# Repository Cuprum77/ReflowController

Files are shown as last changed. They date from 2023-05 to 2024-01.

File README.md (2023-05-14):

# Reflow Controller

This is my own take at building my own reflow oven. This repo will contain all the documentation, code and hardware design files.

## Oven

As there are no easily available small oven here in Norway for a reasonable price, I settled on the [Point PMO16BL](https://www.power.no/kjoekkenmaskiner/kjoekkenapparater/miniovn-og-frittstaaende-platetopp/point-pmo16bl-miniovn/p-1136808/) from Power, a Norwegian electronics store. It's a 16L oven with a max temperature of 230°C. However I do believe we can get it to go higher than that.

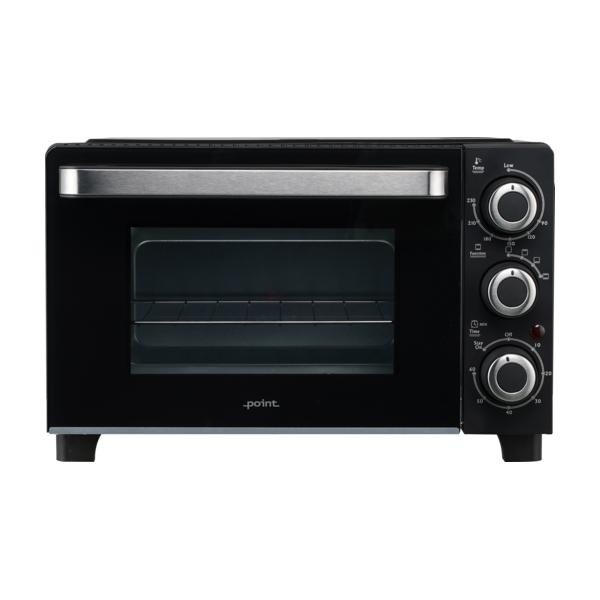
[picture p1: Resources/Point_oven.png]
Oven


Through coupons and discounts I managed to get one brand new from a store for as little as 291 NOK, which as of now (2023-05-14) is about 20.54 USD.

## Controller

The controller itself is designed to be as simple as possible and have to navigate around the still ongoing chip shortage. It features an RP2040 microcontroller, a 1.28" circular LCD display, a button, and the option for a rotary encoder as well as up to 3 thermocouple inputs and 3 relays for controlling the oven.

However, it is not capable of receiving the thermocouples straight in, even though it would have been more practical. This is due to the chips chosen were not available on their own, but only as a breakout board. So to save time and effort, I decided against simply moving the chips over to a main board, and instead just use the breakout boards as is. An advantage of this approach, is the potential for a solderless experience if more thermocouples are needed in the future.

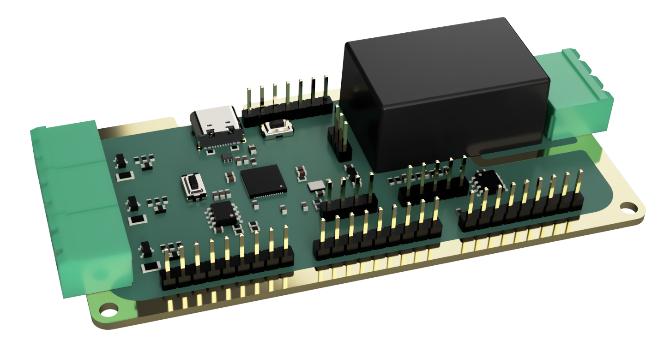
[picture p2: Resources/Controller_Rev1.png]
Controller


The controller will also feature an onboard EEPROM for storing the heat profiles and settings as well as a USB-C connector for programming. The board can be powered directly from mains through a large plug in connector.

## Software

## License
This project is licensed under the CERN Open Hardware Licence v2 - Strong Reciprocity (CERN-OHL-S-2.0). See [LICENSE](./LICENSE) for more information.

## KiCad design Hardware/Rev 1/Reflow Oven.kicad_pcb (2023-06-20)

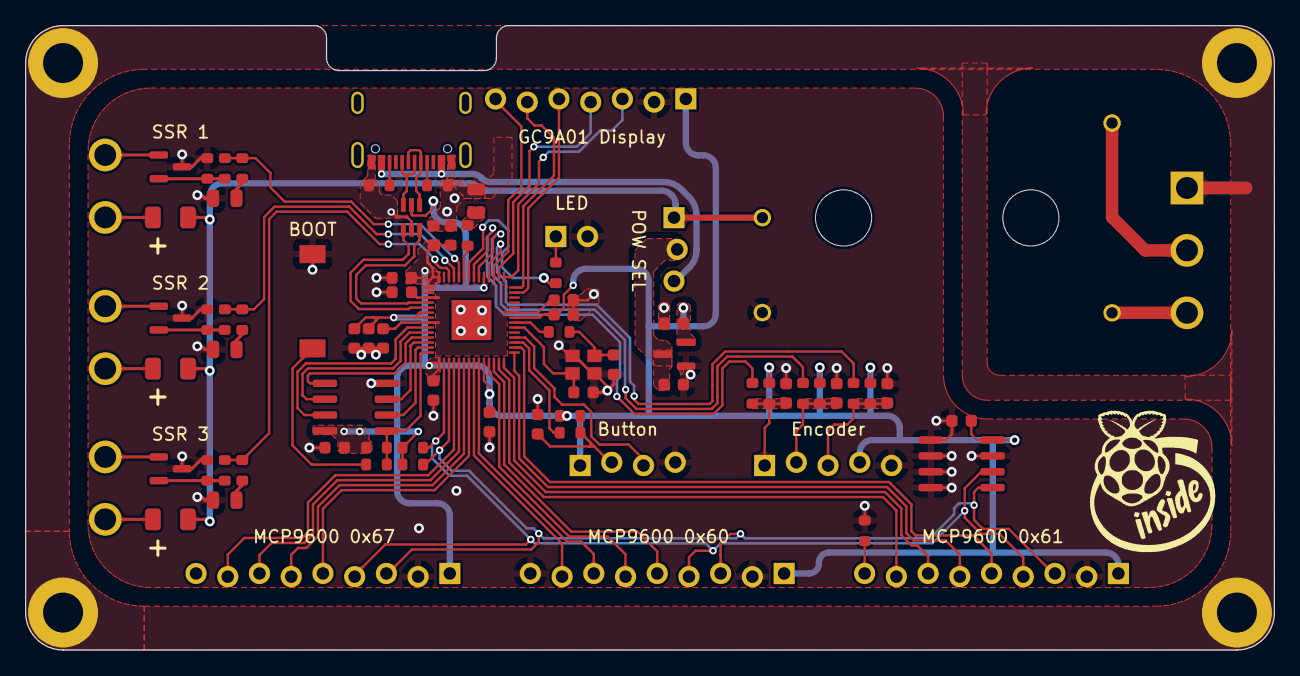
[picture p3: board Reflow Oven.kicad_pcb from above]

Board: 2 copper layers, 100.0 x 50.0 mm, 83 parts (0 on the bottom side), 73 nets.

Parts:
C1, C2, C3, C4: 10n; C_0603_1608Metric
C5, C8, C10, C11, C12, C13, C14, C16, C17, C18, C20: 100n; C_0603_1608Metric
C6, C7: 8p; C_0603_1608Metric
C9, C19: 1u; C_0603_1608Metric
C15: 10u; C_0603_1608Metric
C21: 2u2; C_0603_1608Metric
D1, D2, D3, D4: Red; D_0805_2012Metric
F1, F2, F3: Fuse; Fuse_1206_3216Metric
H1, H2, H3, H4: M3; MountingHole_3.2mm_M3_DIN965_Pad
IC1: MCP1792T; SOT-23
J1: SW; PinHeader_1x04_P2.54mm_Vertical
J2: ENC; PinHeader_1x05_P2.54mm_Vertical
J3, J4, J5: Adafruit 4101; PinHeader_1x09_P2.54mm_Vertical
J6: GC9A01 1.28" TFT; PinHeader_1x07_P2.54mm_Vertical
J7: 2350513-3
J8, J9, J10: 2350513-2
J11: USB4110-GF-A_REVB; USB_C_Receptacle_GCT_USB4105-xx-A_16P_TopMnt_Horizontal
J12: POW_SEL; PinHeader_1x03_P2.54mm_Vertical
J13: Conn_01x02; PinHeader_1x02_P2.54mm_Vertical
P1: IRM015
Q1, Q2, Q3: IRLML2060; SOT-23
R1, R23, R24: 2k2; R_0603_1608Metric
R2, R3, R4, R5, R6, R7, R8, R9, R14, R17, R20: 10k; R_0603_1608Metric
R10, R11: 5k1; R_0603_1608Metric
R12, R15, R18, R26, R27: 270; R_0603_1608Metric
R13, R16, R19: 100; R_0603_1608Metric
R21, R22: DNF; R_0603_1608Metric
R25: 1k; R_0603_1608Metric
SW1: DNF; PTS636 SM25J SMTR LFS
U1: USBUF02W6; SOT65P210X110-6N
U2: W25Q16JV; SOIC-8_3.9x4.9mm_P1.27mm
U3: FT24C04A; SOIC-8_3.9x4.9mm_P1.27mm
U4: RP2040; QFN-56-1EP_7x7mm_P0.4mm_EP3.2x3.2mm
Y1: 12MHz; Crystal_SMD_2520-4Pin_2.5x2.0mm

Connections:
+1V1: C5.1, C8.1, C9.1, U4.23 (DVDD), U4.45 (VREG_VOUT), U4.50 (DVDD)
+3V3: C10.1, C11.1, C12.1, C13.1, C14.1, C16.1, C17.1, C18.1, C19.1, C20.1, C21.1, IC1.2, J1.1, J2.4, J3.1, J4.1, J5.1, J6.1, R2.1, R3.1, R5.1, R8.1, R22.2, R23.1, R24.1, U1.5 (3V3), U2.8 (VCC), U3.8 (VCC), U4.1 (IOVDD), U4.10 (IOVDD), U4.22 (IOVDD), U4.33 (IOVDD), U4.42 (IOVDD), U4.43 (ADC_AVDD), U4.44 (VREG_IN), U4.48 (USB_VDD), U4.49 (IOVDD)
+5V: F1.1, F2.1, F3.1, J12.1, P1.1 (V+)
/ALARM1A: J3.5, U4.7 (GPIO5)
/ALARM1B: J4.5, U4.16 (GPIO13)
/ALARM1C: J5.5, U4.12 (GPIO9)
/ALARM2A: J3.6, U4.6 (GPIO4)
/ALARM2B: J4.6, U4.15 (GPIO12)
/ALARM2C: J5.6, U4.11 (GPIO8)
/ALARM3A: J3.7, U4.5 (GPIO3)
/ALARM3B: J4.7, U4.14 (GPIO11)
/ALARM3C: J5.7, U4.9 (GPIO7)
/ALARM4A: J3.8, U4.4 (GPIO2)
/ALARM4B: J4.8, U4.13 (GPIO10)
/ALARM4C: J5.8, U4.8 (GPIO6)
/Button Filter/SW_OUT: R9.1, U4.17 (GPIO14)
/ENC_A: C1.1, J2.1, R2.2, R4.2
/ENC_B: C2.1, J2.2, R3.2, R6.2
/ENC_Filter/ENC_A_OUT: R4.1, U4.35 (GPIO23)
/ENC_Filter/ENC_B_OUT: R6.1, U4.34 (GPIO22)
/ENC_Filter/ENC_SW_OUT: R7.1, U4.32 (GPIO21)
/ENC_SW: C3.1, J2.3, R5.2, R7.2
/LCD_CS: J6.6, U4.28 (GPIO17)
/LCD_D/C: J6.5, U4.27 (GPIO16)
/LCD_MOSI: J6.4, U4.30 (GPIO19)
/LCD_RST: J6.7, U4.31 (GPIO20)
/LCD_SCK: J6.3, U4.29 (GPIO18)
/Live: J7.2, P1.4 (L)
/MOSFET_1: R12.1, R13.1, U4.40 (GPIO28_ADC2)
/MOSFET_2: R15.1, R16.1, U4.38 (GPIO26_ADC0)
/MOSFET_3: R18.1, R19.1, U4.39 (GPIO27_ADC1)
/MOSFETs/SSR_1: J8.2, Q1.1 (D)
/MOSFETs/SSR_1_COM: F1.2, J8.1
/MOSFETs/SSR_2: J9.2, Q2.1 (D)
/MOSFETs/SSR_2_COM: F2.2, J9.1
/MOSFETs/SSR_3: J10.2, Q3.1 (D)
/MOSFETs/SSR_3_COM: F3.2, J10.1
/Microcontroller Alarm/LED_ACTIVE: R26.2, U4.37 (GPIO25)
/Microcontroller Alarm/LED_FRONT: R27.2, U4.36 (GPIO24)
/Microcontroller Alarm/QSPI_SCLK: U2.6 (CLK), U4.52 (QSPI_SCLK)
/Microcontroller Alarm/QSPI_SD0: U2.5 (DI(IO0)), U4.53 (QSPI_SD0)
/Microcontroller Alarm/QSPI_SD1: U2.2 (DO(IO1)), U4.55 (QSPI_SD1)
/Microcontroller Alarm/QSPI_SD2: U2.3 (IO2), U4.54 (QSPI_SD2)
/Microcontroller Alarm/QSPI_SD3: U2.7 (IO3), U4.51 (QSPI_SD3)
/Microcontroller Alarm/QSPI_SS: R21.2, R22.1, U2.1 (~CS), U4.56 (QSPI_SS)
/Microcontroller Alarm/SW_LED: J1.3, U4.18 (GPIO15)
/Microcontroller Alarm/USB_D+: U1.1 (D+), U4.47 (USB_DP)
/Microcontroller Alarm/USB_D-: U1.3 (D-), U4.46 (USB_DM)
/Microcontroller Alarm/XIN: C6.2, U4.20 (XIN), Y1.1
/Microcontroller Alarm/XOUT: R25.1, U4.21 (XOUT)
/Neutral: J7.3, P1.3 (N)
/SCL: J3.3, J4.3, J5.3, R24.2, U3.5 (SDA), U4.3 (GPIO1)
/SDA: J3.4, J4.4, J5.4, R23.2, U3.6 (SCL), U4.2 (GPIO0)
/SW: C4.1, J1.2, R8.2, R9.2
/USB/USB_PRE_D+: J11.A6 (D+), J11.B6 (D+), U1.6 (D+)
/USB/USB_PRE_D-: J11.A7 (D-), J11.B7 (D-), U1.4 (D-)
Earth: H1.1, H2.1, H3.1, H4.1, J7.1
GND: C1.2, C2.2, C3.2, C4.2, C5.2, C6.1, C7.1, C8.2, C9.2, C10.2, C11.2, C12.2, C13.2, C14.2, C15.2, C16.2, C17.2, C18.2, C19.2, C20.2, C21.2, D1.1 (K), D2.1 (K), D3.1 (K), D4.1 (K), IC1.1, J1.4, J2.5, J3.2, J4.2, J5.2, J5.9, J6.2, J11.A1/B12 (GND), J11.B1/A12 (GND), J13.2, P1.2 (V-), Q1.3 (S), Q2.3 (S), Q3.3 (S), R1.1, R10.2, R11.2, R14.2, R17.2, R20.2, SW1.1, U1.2 (Grd), U2.4 (GND), U3.1 (A0), U3.2 (A1), U3.3 (A3), U3.4 (GND), U3.7 (WP), U4.57 (GND), Y1.2, Y1.4
unnamed: C7.2, R25.2, Y1.3
unnamed: D1.2 (A), R12.2
unnamed: D2.2 (A), R15.2
unnamed: D3.2 (A), R18.2
unnamed: D4.2 (A), R26.1
unnamed: J4.9, R1.2
unnamed: J11.A5 (CC1), R10.1
unnamed: J11.B5 (CC2), R11.1
unnamed: C15.1, IC1.3, J12.2
unnamed: J13.1, R27.1
unnamed: Q1.2 (G), R13.2, R14.1
unnamed: Q2.2 (G), R16.2, R17.1
unnamed: Q3.2 (G), R19.2, R20.1
unnamed: R21.1, SW1.2
VBUS: J11.A4/B9 (VBUS), J11.B4/A9 (VBUS), J12.3

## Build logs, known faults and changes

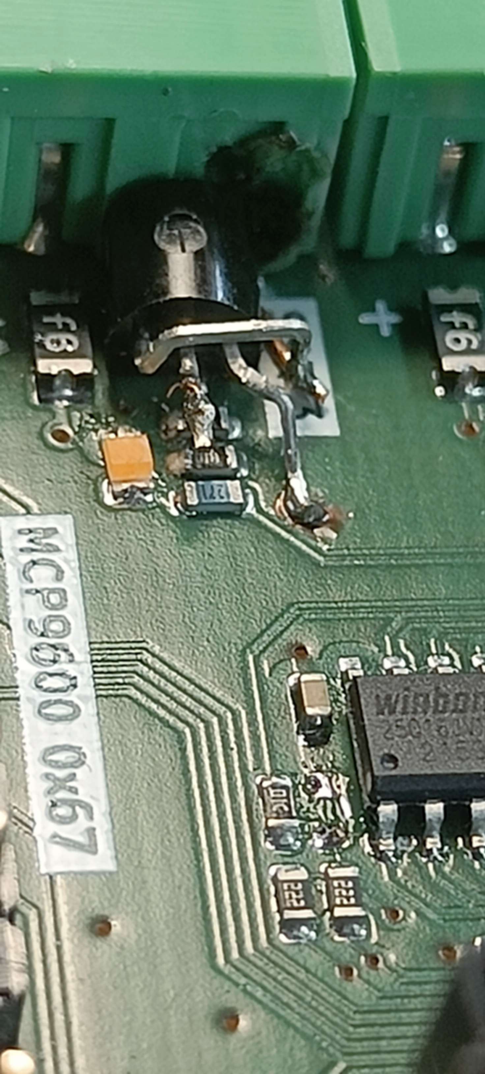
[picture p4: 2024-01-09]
Resources/rev1_fix.jpg

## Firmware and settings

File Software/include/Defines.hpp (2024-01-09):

// This is a header guard. It prevents the file from being included more than once.
#pragma once

/***
 *      ____  _           
 *     |  _ \(_)_ __  ___ 
 *     | |_) | | '_ \/ __|
 *     |  __/| | | | \__ \
 *     |_|   |_|_| |_|___/
 *                        
 */

// Alarm pins
#define ALARM_PIN_1_A 5
#define ALARM_PIN_2_A 4
#define ALARM_PIN_3_A 3
#define ALARM_PIN_4_A 2

#define ALARM_PIN_1_B 13
#define ALARM_PIN_2_B 12
#define ALARM_PIN_3_B 11
#define ALARM_PIN_4_B 10

#define ALARM_PIN_1_C 9
#define ALARM_PIN_2_C 8
#define ALARM_PIN_3_C 7
#define ALARM_PIN_4_C 6

// I2C pins
#define I2C_SDA 0
#define I2C_SCL 1

// Button pins
#define BUTTON_PIN 14
#define BUTTON_LED_PIN 15

// Display pins
#define DISPLAY_DC 16
#define DISPLAY_CS 17
#define DISPLAY_SCK 18
#define DISPLAY_MOSI 19
#define DISPLAY_RST 20
#define DISPLAY_BL -1

// Encouder pins
#define ENCODER_A 23
#define ENCODER_B 22
#define ENCODER_SW 21

// Status LEDs
#define LED_BUILDIN 25
#define LED_FRONT 24

// Output Enable
#define OUTPUT_ENABLE_1_PIN 26
#define OUTPUT_ENABLE_2_PIN 27
#define OUTPUT_ENABLE_3_PIN 28


/***
 *     __     __         _       _     _           
 *     \ \   / /_ _ _ __(_) __ _| |__ | | ___  ___ 
 *      \ \ / / _` | '__| |/ _` | '_ \| |/ _ \/ __|
 *       \ V / (_| | |  | | (_| | |_) | |  __/\__ \
 *        \_/ \__,_|_|  |_|\__,_|_.__/|_|\___||___/
 *                                                 
 */

// Temperature defines (in °C)
#define LOWEST_TEMPERATURE 20       // Room temperature, no real need to go lower (Only used to set the gauge range)
#define CRITICAL_TEMPERATURE 250    // Max temperature the oven should withstand, NEVER EXCEED 300°C!

// I2C Speed
#define I2C_SPEED 100000

// Display
#define DISPLAY_WIDTH 240
#define DISPLAY_HEIGHT 240
#define DISPLAY_OFFSET_X0 0
#define DISPLAY_OFFSET_X1 0
#define DISPLAY_OFFSET_Y0 0
#define DISPLAY_OFFSET_Y1 0
#define DISPLAY_ROTATION 2  // 0 = horizontal, 1 = portrait, 2 = flipped horizontal, 3 = flipped portrait

// PID Control loop
#define DEFAULT_KP 1.25f
#define DEFAULT_KI 0.00f
#define DEFAULT_KD 0.00f
#define DEFAULT_DT 0.02f
#define DEFAULT_MIN -127.0f
#define DEFAULT_MAX 127.0f
#define DEFAULT_TOLERANCE 0.1f


/***
 *         _       _     _                             
 *        / \   __| | __| |_ __ ___  ___ ___  ___  ___ 
 *       / _ \ / _` |/ _` | '__/ _ \/ __/ __|/ _ \/ __|
 *      / ___ \ (_| | (_| | | |  __/\__ \__ \  __/\__ \
 *     /_/   \_\__,_|\__,_|_|  \___||___/___/\___||___/
 *                                                     
 */

// MCP9600 Breakout boards
#define MCP9600_1_ADDRESS 0x61
#define MCP9600_2_ADDRESS 0x60  
#define MCP9600_3_ADDRESS 0x67

// EEPROM IC
#define EEPROM_ADDRESS 0x50


/***
 *      ___            _           _           
 *     |_ _|_ __   ___| |_   _  __| | ___  ___ 
 *      | || '_ \ / __| | | | |/ _` |/ _ \/ __|
 *      | || | | | (__| | |_| | (_| |  __/\__ \
 *     |___|_| |_|\___|_|\__,_|\__,_|\___||___/
 *                                             
 */

#include <stdio.h>
#include <stdlib.h>
#include "pico/stdlib.h"
#include "pico/bootrom.h"
#include "pico/binary_info.h"
#include "pico/multicore.h"
#include "hardware/uart.h"
#include "hardware/i2c.h"
#include "hardware/watchdog.h"
#include "tusb.h"

#include "Button.hpp"
#include "Memory.hpp"
#include "MCP9600.hpp"
#include "version.h"
#include "PicoGFX.hpp"
#include "ComicSans48.font"
#include "ComicSans24.font"

#include "heatmap.h"
#include "error.hpp"
#include "oven.hpp"
#include "rotaryEncoder.hpp"
#include "menu.hpp"


/***
 *      ____  _         _____           _    ____        _        
 *     |  _ \(_) ___ __|_   _|__   ___ | |  |  _ \  __ _| |_ __ _ 
 *     | |_) | |/ __/ _ \| |/ _ \ / _ \| |  | | | |/ _` | __/ _` |
 *     |  __/| | (_| (_) | | (_) | (_) | |  | |_| | (_| | || (_| |
 *     |_|   |_|\___\___/|_|\___/ \___/|_|  |____/ \__,_|\__\__,_|
 *                                                               
 */

bi_decl(bi_program_name("Reflow Oven Controller"));
bi_decl(bi_program_description("Pico based PID controller for a reflow oven with temperature monitoring and control."));
bi_decl(bi_program_version_string(GIT_COMMIT_HASH));
bi_decl(bi_program_url("https://github.com/Cuprum77/ReflowController"));

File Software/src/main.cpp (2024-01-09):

#include "include/defines.hpp"

// set the display parameters
Display_Pins displayPins = {
	.rst = DISPLAY_RST,
	.dc = DISPLAY_DC,
	.cs = DISPLAY_CS,
	.sda = DISPLAY_MOSI,
	.scl = DISPLAY_SCK,
};

Hardware_Params hardwareParams = {
	.hw_interface = SPI_Interface_t::PIO_HW,
	.spi_instance = nullptr,
	.baudrate = 125000000,
};

Display_Params displayParams = {
	.type = display_type_t::GC9A01,
	.height = DISPLAY_HEIGHT,
	.width = DISPLAY_WIDTH,
	.columnOffset1 = DISPLAY_OFFSET_X0,
	.columnOffset2 = DISPLAY_OFFSET_X1,
	.rowOffset1 = DISPLAY_OFFSET_Y0,
	.rowOffset2 = DISPLAY_OFFSET_Y1,
	.rotation = DISPLAY_ROTATION
};

// Create the display object
HardwareSPI spi(displayPins, hardwareParams);
Display display(&spi, &displayPins, &displayParams);
// Create the GFX objects
Print print(display.getFrameBuffer(), displayParams);
Graphics graphics(display.getFrameBuffer(), displayParams);
// Create the PicoGFX object
PicoGFX picoGFX(&display, &print, &graphics, nullptr, nullptr);

// Create the peripheral objects
Memory memory(EEPROM_ADDRESS, i2c0);
MCP9600 mcp9600_1(MCP9600_1_ADDRESS, i2c0);
MCP9600 mcp9600_2(MCP9600_2_ADDRESS, i2c0);
MCP9600 mcp9600_3(MCP9600_3_ADDRESS, i2c0);
Button button(BUTTON_PIN, true);
RotaryEncoder encoder(ENCODER_A, ENCODER_B, ENCODER_SW, CRITICAL_TEMPERATURE);

// Create the oven objects
PID pid(DEFAULT_KP, DEFAULT_KI, DEFAULT_KD, DEFAULT_DT, DEFAULT_MIN, DEFAULT_MAX, DEFAULT_TOLERANCE);
Oven oven(&pid, &mcp9600_1, &mcp9600_2, &mcp9600_3, OUTPUT_ENABLE_1_PIN, OUTPUT_ENABLE_2_PIN, OUTPUT_ENABLE_3_PIN, LED_FRONT);
Menu menu(&picoGFX, &oven, &encoder, &ComicSans48, &ComicSans24);

// Declare variables for the timer loops
unsigned long runOccasionallyLastTime = 0;
unsigned long blinkLastTime = 0;
int targetTemperature = 0;
bool blink = false;
bool runOven = false;
bool prevButtonState = false;
bool EEPROM_isConnected = false;

// Handle the variables for the dial gauges
static Color setPointColors[2] = { Colors::White, Colors::Red };
size_t setPointColorSize = sizeof(setPointColors) / sizeof(setPointColors[0]);
Point center = picoGFX.getDisplay().getCenter();
int width = picoGFX.getDisplay().getWidth();
int height = picoGFX.getDisplay().getHeight();
int radius = picoGFX.getDisplay().getWidth() >> 1;

// Create a dial gauge object based on the display
DialGauge temperatureGauge(&graphics, width, height, center, radius, LOWEST_TEMPERATURE, 
	CRITICAL_TEMPERATURE, heatmap, heatmapSize, DialGaugeType_t::DialSimple);
// Create another dial for the set point menu
DialGauge setPointGauge(&graphics, width, height, center, radius, LOWEST_TEMPERATURE, 
	CRITICAL_TEMPERATURE, setPointColors, setPointColorSize, DialGaugeType_t::DialSimple2);

// Keep track of the menu state
menuState_t menuState = menuState_t::menuTemperature;

void main1()
{
	// Wait for the other core to be ready
	while(!multicore_fifo_pop_blocking()) tight_loop_contents();

	// Attach the temperature gauge to the menu
	menu.attachTemperatureGauge(&temperatureGauge);
	menu.attachSetPointGauge(&setPointGauge);

	while(1)
	{
		menu.update(menuState);
	}
}

int main()
{
	// initialize the stdio
	stdio_init_all();

	// initialize the SPI bus and display
	spi.init();
	display.init();
	picoGFX.getGraphics().fill(Colors::Pink);
	picoGFX.getDisplay().update();

	// Initialize the GPIO
	gpio_init(LED_BUILDIN);
	gpio_init(BUTTON_PIN);
	gpio_init(BUTTON_LED_PIN);

	// Set the direction of the GPIO
	gpio_set_dir(LED_BUILDIN, GPIO_OUT);
	gpio_set_dir(BUTTON_PIN, GPIO_IN);
	gpio_set_dir(BUTTON_LED_PIN, GPIO_OUT);

	// initialize the I2C0 bus
	gpio_set_function(I2C_SDA, GPIO_FUNC_I2C);
	gpio_set_function(I2C_SCL, GPIO_FUNC_I2C);
	gpio_pull_up(I2C_SDA);
	gpio_pull_up(I2C_SCL);
	i2c_init(i2c0, I2C_SPEED);
	// set the binary data to show the pins used for I2C0
	bi_decl(bi_2pins_with_func(I2C_SDA, I2C_SCL, GPIO_FUNC_I2C));

	// verify that the EEPROM is connected
	EEPROM_isConnected = memory.verifyConnection();

	// enable watchdog requiring a reset every 500ms
	watchdog_enable(500, 1);

	// setup the second core
	multicore_launch_core1(main1);

	// Initialize the oven
	oven.init(heaters_t::HEATER_3);
	// Update the watchdog just in case
	watchdog_update();

	// Tell the other core that they can start
	multicore_fifo_push_blocking(1);
	
	while(1)
	{
		// sleep for 10ms to avoid damaging the relay through PID seizures
		if((time_us_64() - runOccasionallyLastTime) >= 10000)
		{
			// Check if the button was clicked
			if(button.isClicked())
				runOven = !runOven;
			// Update the button led
			gpio_put(BUTTON_LED_PIN, runOven);

			oven.updateHeaters(runOven, 50);
			runOccasionallyLastTime = time_us_32();
		}

		// blink the leds
		if((time_us_64() - blinkLastTime) >= 500000)
		{
			gpio_put(LED_BUILDIN, !blink);
			blink = !blink;
			blinkLastTime = time_us_32();
		}

		// Update the encoder
		encoder.update();
		
		// Update the button
		button.update();

		// Kick the watchdog
		watchdog_update();
	}
}

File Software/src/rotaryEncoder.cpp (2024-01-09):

#include "rotaryEncoder.hpp"

/**
 * @brief Construct a new Rotary Encoder object
 * @param pinA The pin connected to the A output of the rotary encoder
 * @param pinB The pin connected to the B output of the rotary encoder
 * @param buttonPin The pin connected to the button output of the rotary encoder
 * @param upperLimit The upper limit of the counter, default is CRITICAL_TEMPERATURE. If we reach this value, we overflow to 0
*/
RotaryEncoder::RotaryEncoder(int pinA, int pinB, int buttonPin, int upperLimit)
{

}

/**
 * @brief Initialize the rotary encoder object
*/
void RotaryEncoder::init()
{

}

/**
 * @brief Update the rotary encoder object
 * @note This function should be called in the main loop
*/
void RotaryEncoder::update()
{

}

/**
 * @brief Get the button state
 * @return true if the button is pressed, false otherwise
*/
bool RotaryEncoder::getButton()
{
    return false;
}

/**
 * @brief Reset the encoder value
*/
void RotaryEncoder::resetEncoderValue()
{
    this->encoderValue = 0;
}

/**
 * @brief Get the encoder position
 * @return The value of the encoder
*/
int RotaryEncoder::getEncoderValue()
{
    return this->encoderValue;
}

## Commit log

2023-05-13 minor work left on rev1
    [Button Filter.kicad_sch, Display.kicad_sch, ENC_Filter.kicad_sch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]
2023-05-13 minor tweaks
    [Reflow Oven.kicad_pcb, USB.kicad_sch]
2023-05-13 pin definitions
2023-05-13 fixing potential acid traps
    [Reflow Oven.kicad_pcb]
2023-05-14 changed i2c pins to match current development
2023-05-14 removed gerber for now
2023-05-18 i dont know what im doing wrong
    [main.cpp]
2023-05-19 moved display driver to its own repo
2023-05-23 functional prototype
    [MicrocontrollerAlarm.kicad_sch, Reflow Oven.kicad_pcb]
2023-06-07 small pcb improvements
    [Reflow Oven.kicad_pcb]
2023-06-13 redid 2 layer, thanks git
    [Reflow Oven.kicad_pcb]
2023-06-13 ordered from aisler
    [MicrocontrollerAlarm.kicad_sch, Reflow Oven.kicad_pcb]
2023-06-13 solder mask missing!
    [Reflow Oven.kicad_pcb]
2023-06-13 added date
    [Reflow Oven.kicad_pcb]
2023-06-20 added missing teardrops
    [Reflow Oven.kicad_pcb]
2023-06-20 minor fixes
    [Reflow Oven.kicad_pcb]
2023-07-04 added BOM
2023-08-15 updated the schematic with the value for R21
    [MicrocontrollerAlarm.kicad_sch]
2023-08-15 rotary encoder class placeholder
2023-08-15 added the button library from the PD project
2023-08-15 moved heatmap to its own file
2023-08-15 cleanup and fixing race conditions
    [main.cpp, menu.cpp, oven.cpp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]
2023-08-17 fixed the oven problem
    [main.cpp, oven.cpp, oven.hpp]
2024-01-09 added a basic plotter to see temperature real time
